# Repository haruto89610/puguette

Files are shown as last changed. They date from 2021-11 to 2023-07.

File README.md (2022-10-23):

# Puguette (パゲット)

[instagram](https://www.instagram.com/haruto89610/)

[photos](https://photos.app.goo.gl/W3VdmgdQKvAVjbRc6)

[twitter](https://twitter.com/TofuTohuman)

[Japanese](./README_jp.md)

[Youtube explanation in Japanese](https://www.youtube.com/watch?v=FokTPg63v5w)


|||
|:---|:---|
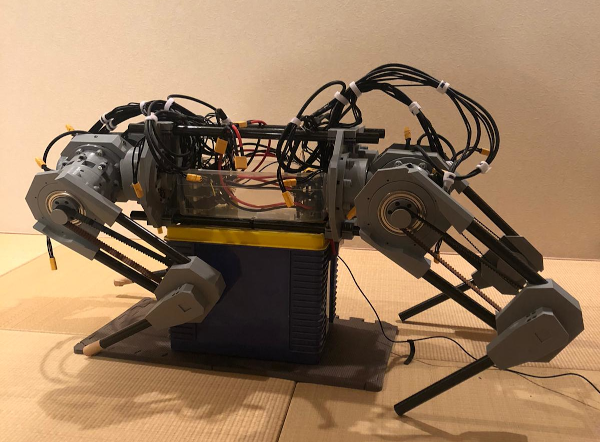
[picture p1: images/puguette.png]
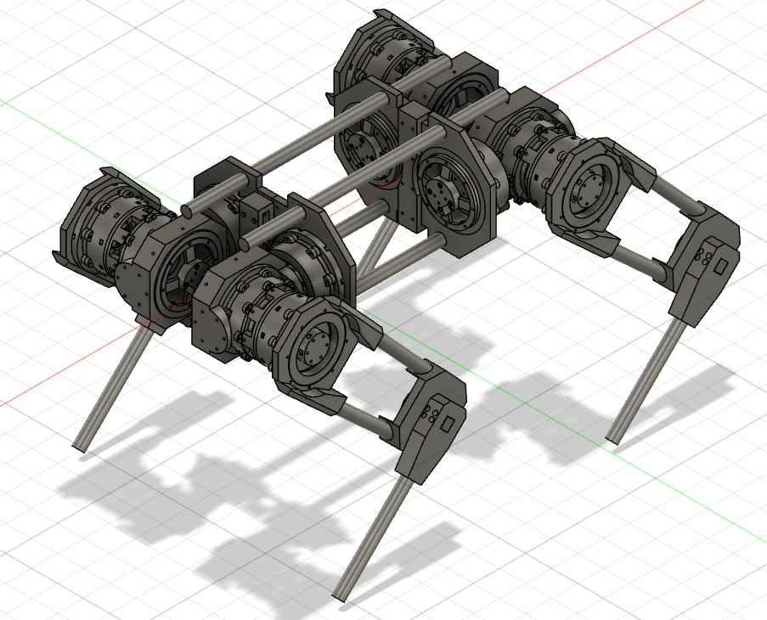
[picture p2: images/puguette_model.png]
|<p>(In progress)</p>|<p>(3D model)</p>|

## Introduction

Puguette is a fully open source 12 DOF quadruped robot. It stands at 80cm x 40cm x 60cm (when the legs are straight). It uses a BLDC motor for high torque efficiency and is coupled with a planetary gearbox to further increase said torque. The design is made to make small tweaks easy to change. For example, in order to change the gear ratio, just print the ring gear, planet gear and sun gear with the desired teeth count. Then mount that onto the motor holder. This can be done to the motor holder as well. To control Puguette, a Teensy 3.6, Jetson Nano, and 6 ODrives are used.

## Prototype

The older counterpart of Puguette, Spaghette, uses hobby servo motors. Similar to Puguette, it is 12 DOF and is fully 3D printed. In contrast to Puguette, Spaghette uses only an Arduino Mega to power it.

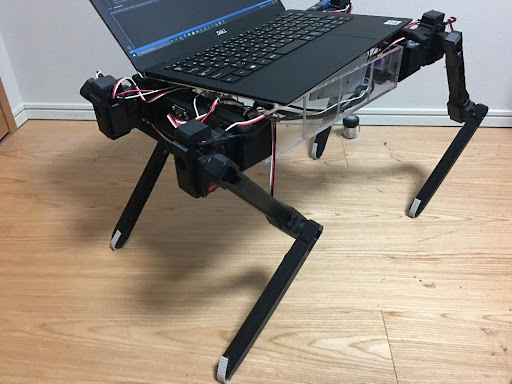
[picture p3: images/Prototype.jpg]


## Architecture

The Jetson Nano is the center of this robot. It communicates with the Teensy 3.6 via USB. The Teensy then communicates with all 6 ODrives using UART.

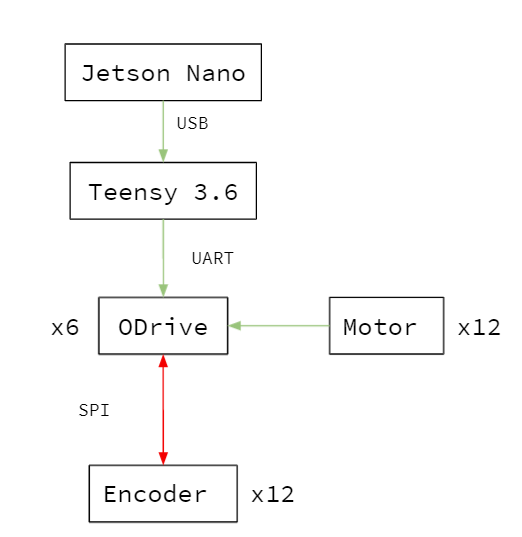
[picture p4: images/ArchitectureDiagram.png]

(architecture mindmap)

## Hardware Specification

There are 2 different (although similar) actuators designed. One for the x8318s motor, and one for the 8308 motor.
The total torque for each actuator is approx. 55Nm. The 8308 motor is connected to a 12:21 chain transmission system to further increase torque.

| Name | Unit | Description |
| :--- | :--- | :--- |
| X8318s motor | 4 | Upper leg actuator motor |
| 8308 motor | 8 | Lower and hip abductor actuator motor |
| ODrive driver | 6 | Controls motor |
| AS5048a encoder | 12 | Measures angle |
| Teensy microcontroller | 1 | Controls ODrive via UART |
| Bearing 6900ZZ | 4 | Bearing for Upper leg actuator |
| Bearing 6000ZZ | 36 | Bearing for planet gears |
| Bearing 6006ZZ | 4 | Bearing for lower joint  |
| Bearing 6010ZZ | 8 | Bearing for 8308 motor actuator |
| Lipo Battery | 3 | Power supply for the robot |

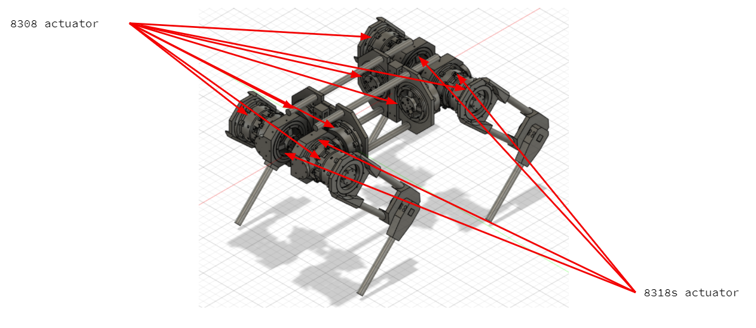
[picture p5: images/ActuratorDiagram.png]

(location of actuators)

## Actuator Assembly

  1. Mount encoder onto encoder holder using m2 screws.
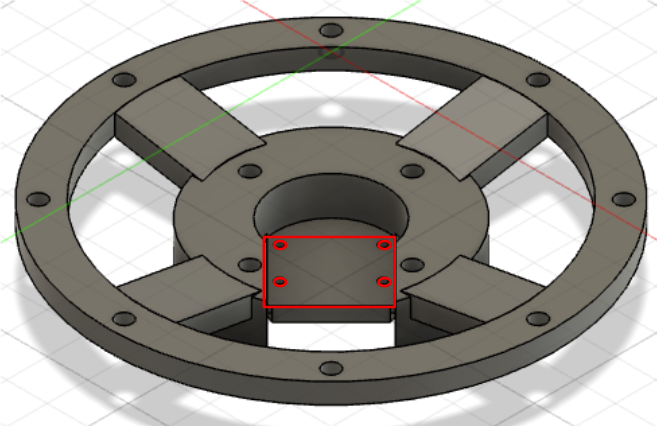
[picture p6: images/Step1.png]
  
  2. Mount the encoder magnet on the motor via the magnet holder.
  3. Insert m4 hex-nuts into the sides of motor holder.
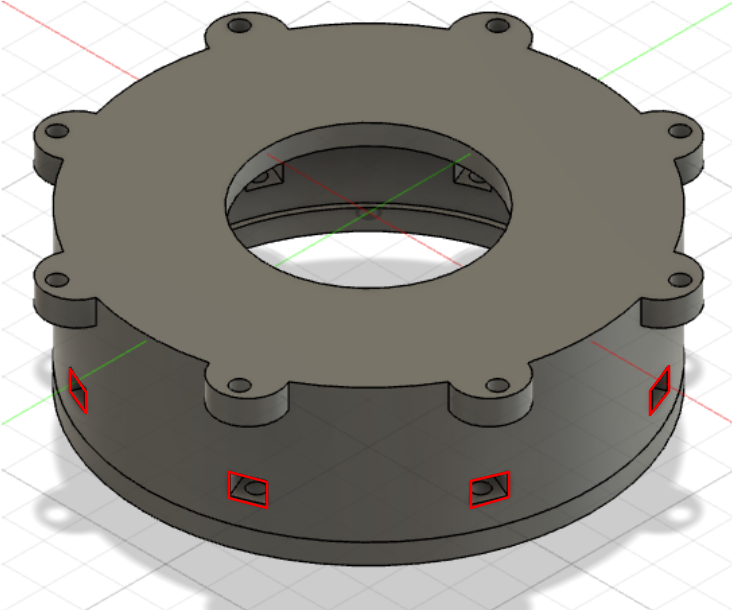
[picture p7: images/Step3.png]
  
  4. Screw encoder holder onto the motor holder via the holes.
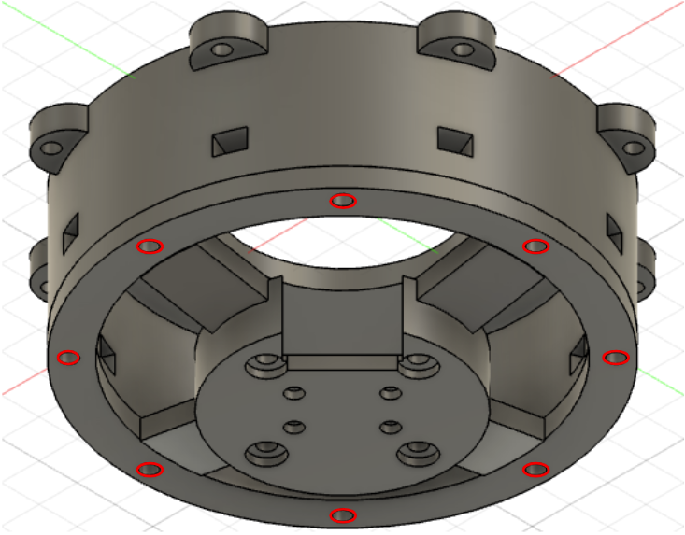
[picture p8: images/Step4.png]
  
  5. Place bearings onto the ring gear, and planet gear.
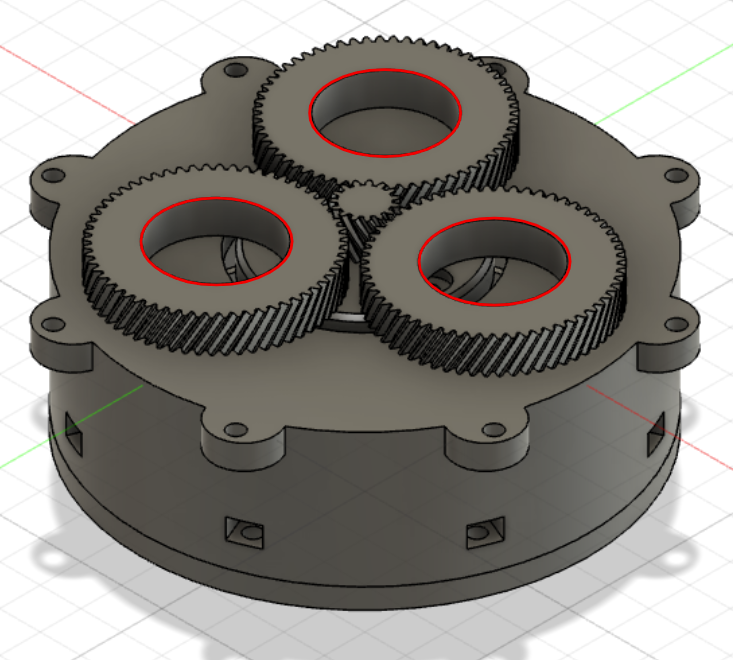
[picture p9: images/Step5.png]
  
  6. Push the planet gear onto the planet gear holder.
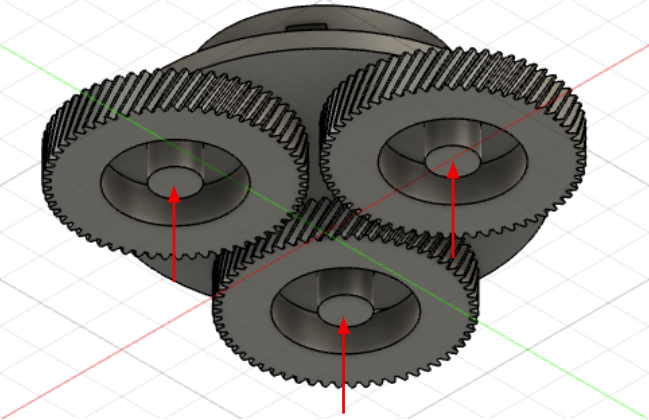
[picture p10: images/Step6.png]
  
  7. Mount the sun gear onto the motor via the opening on the motor holder.
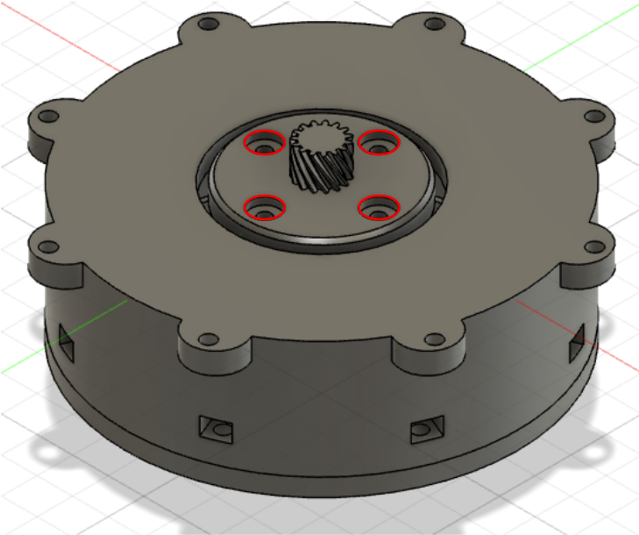
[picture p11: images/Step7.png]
  
  8. Push the sun gear into the center of the planet gear and planet gear holder.
  9. Push the ring gear on top of the planet gear holder.
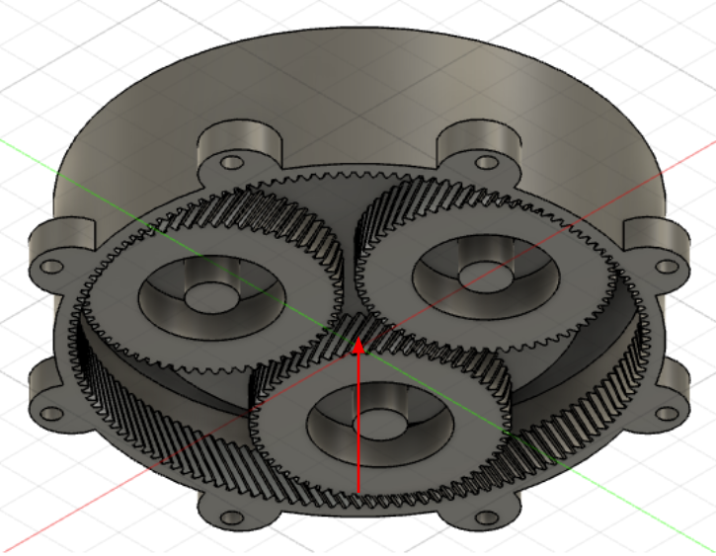
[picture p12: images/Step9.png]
  
  10. Mount motor holder onto ring gear.
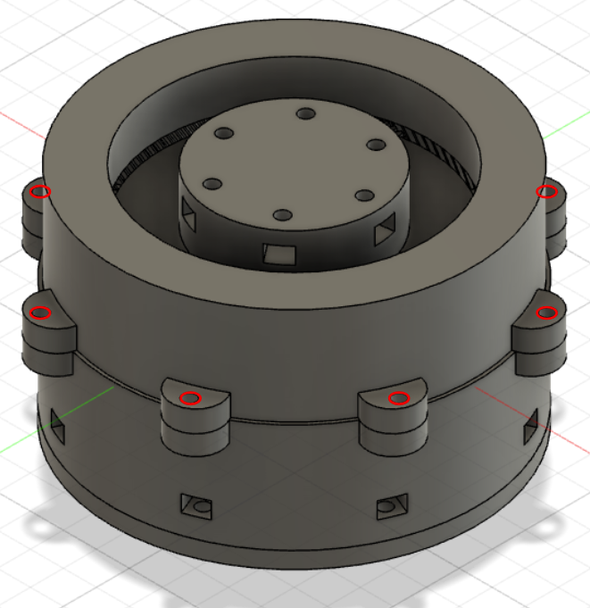
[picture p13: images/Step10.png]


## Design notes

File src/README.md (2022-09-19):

## Software and Simulation

The robot has went through different versions with different architectures. The old version aimed to use a Jetson Nano as well as a Teensy to control the 6 ODrives. As a result, part of the code was written in C++ as well as Python. However, errors were encountered where the UART signals had incorrect values. This could possibly have originated from noise, or the large amount of information needed to be transmitted. Although lowering the baudrate resulted in cleaner results, completely removing the issue was a difficult problem to overcome. As a result, the Teensy was removed, and the Jetson Nano communicates directly with the ODrives via USB. The new program uses only Python.

Because testing the robot is not always easy, considering the sheer size of the robot, a PyBullet simulation was made to attempt to help with testing. Because the polygon count on the actual CAD is too high, rendering the model was an issue. To solve this issue, the simulation uses a simplified version of the CAD model.

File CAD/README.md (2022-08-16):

## Updates

The first iteration of the actuator had many flaws. One of these major flaws was that many parts would break as a result of torsional stress. Most notably, the sun gear, and the planet gear carrier. To counter this, the second iteration of the actuator uses chrome gears to replace the PLA sun gears. These chrome gears have 15 teeth and a gear module of 0.8 (https://www.monotaro.com/p/3682/5512/?t.attr_f957=0.8&t.attr_f958=15&t.q=%83M%83A). As some motors do not have a shaft for the gears to attach to, a sun gear adapter was created to counter this issue. As for the planet gear carriers, the part was split into two different models. The Planet Carrier Bottom connects to the Planet Carrier Top with the planet gear in between. These two parts can then be screwed in place with an M4 screw. Overall, the issue main issue with the first iteration was that the actuator broke under high torque.

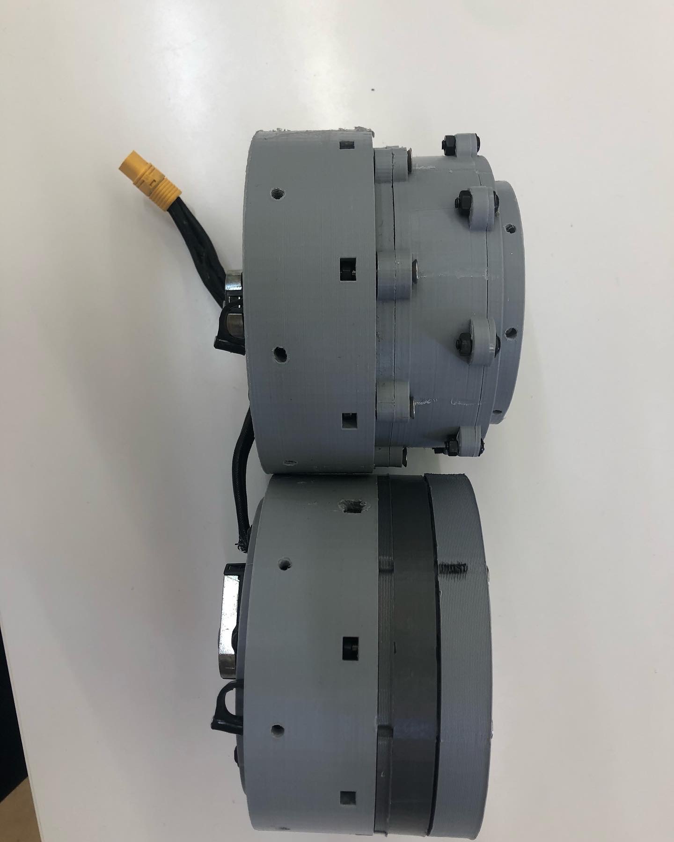
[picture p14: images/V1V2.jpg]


First test of Actuator V2:
https://www.instagram.com/p/Cg_KBtlJQmC/

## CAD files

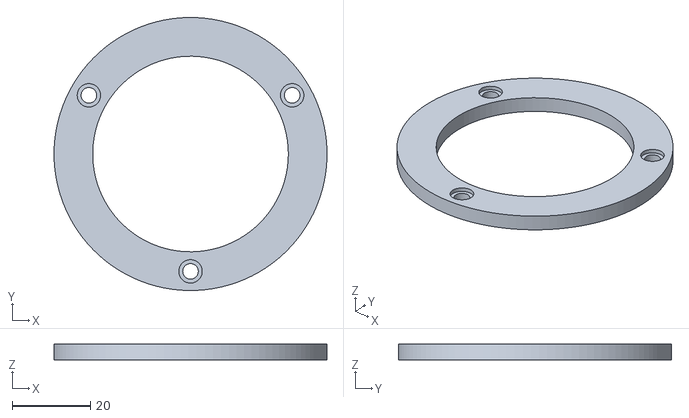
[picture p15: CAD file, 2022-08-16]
CAD/Actuator V2/8308 actuator V2/Planet Carrier Bottom v3.stl
69.8 x 69.8 x 4.00

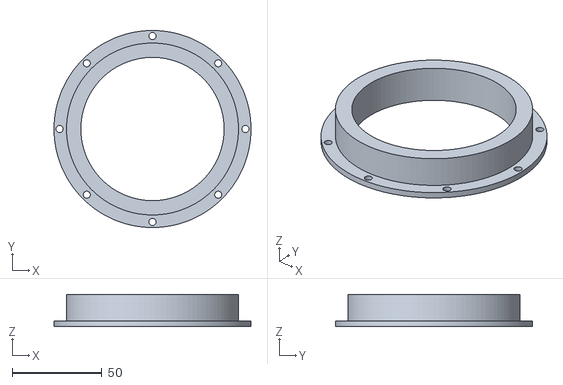
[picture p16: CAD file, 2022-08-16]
CAD/Actuator V2/8318 actuator V2/Ring Gear Cover v7.stl
110.0 x 110.0 x 18.0

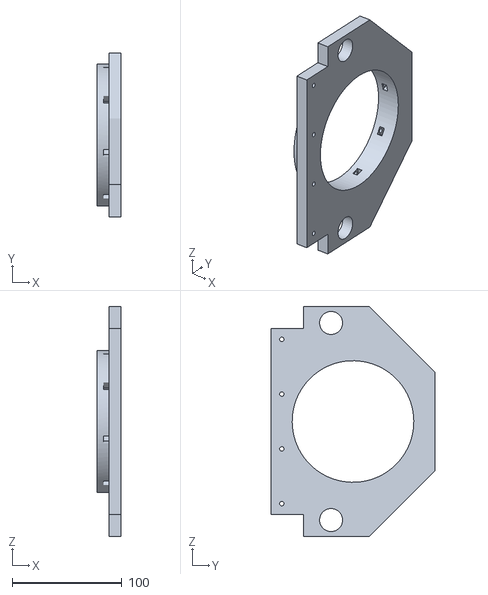
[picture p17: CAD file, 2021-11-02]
CAD/Hip mechanism/Hip Actuator Holder.stl
22.0 x 150.0 x 210.0

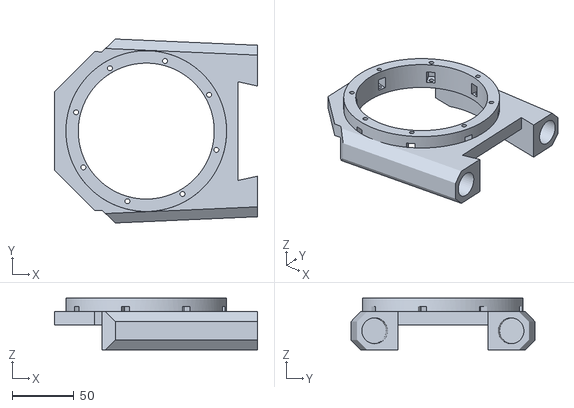
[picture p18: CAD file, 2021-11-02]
CAD/Leg/Upper Leg Holder.stl
164.2 x 148.8 x 42.0

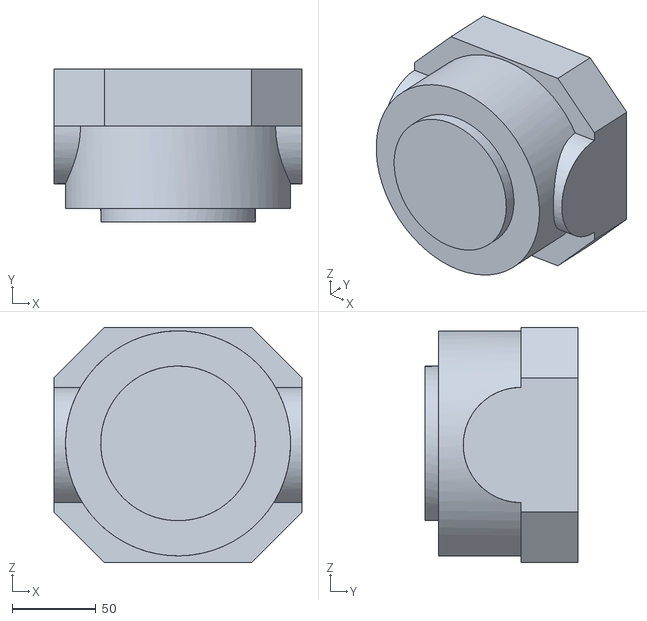
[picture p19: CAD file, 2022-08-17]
src/PyBullet Simulation/meshes/BL_Joint1.stl
147.7 x 91.0 x 140.0

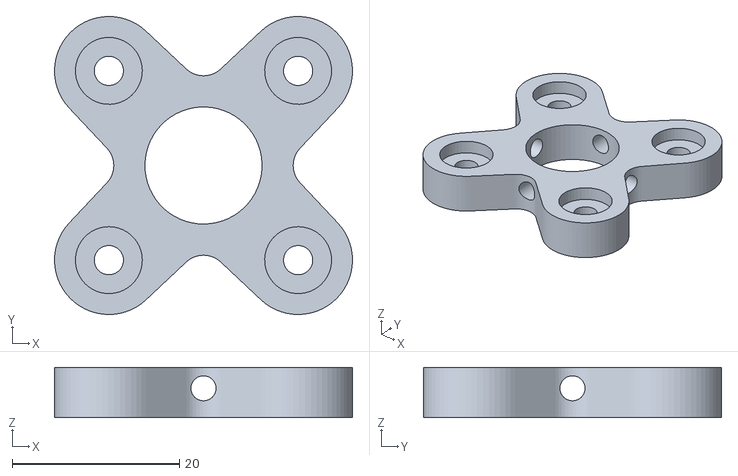
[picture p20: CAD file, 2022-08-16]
CAD/Actuator V2/8308 actuator V2/Sun Gear Adapter v3.stl
35.6 x 35.6 x 6.00

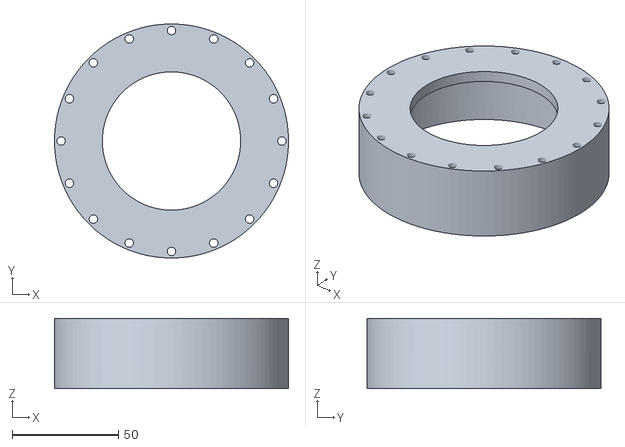
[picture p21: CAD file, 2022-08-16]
CAD/Actuator V2/8318 actuator V2/Motor Holder v6.stl
110.0 x 110.0 x 33.0

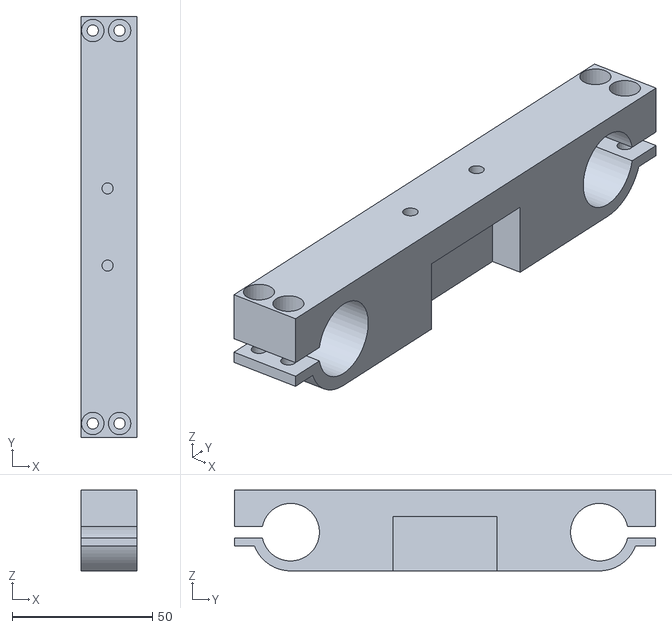
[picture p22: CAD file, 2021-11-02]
CAD/Hip mechanism/Hip Rod Support.stl
20.0 x 150.0 x 28.8

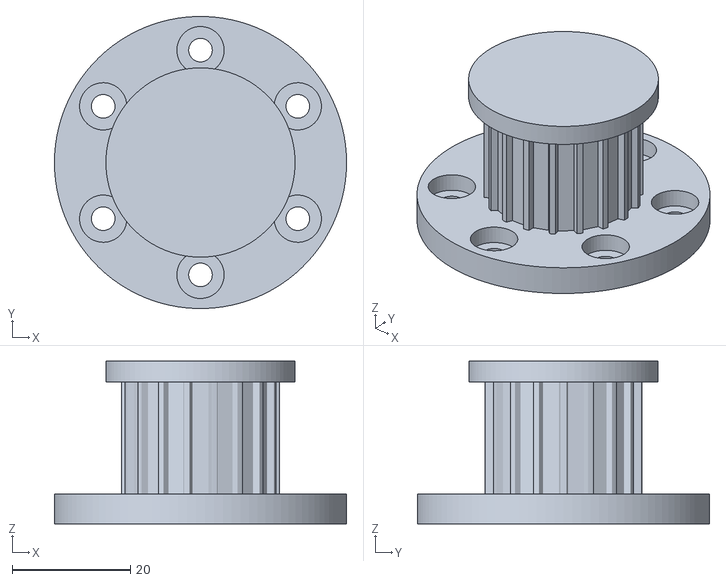
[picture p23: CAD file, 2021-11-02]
CAD/Leg/Upper Leg Timing Pulley.stl
49.4 x 49.4 x 27.5

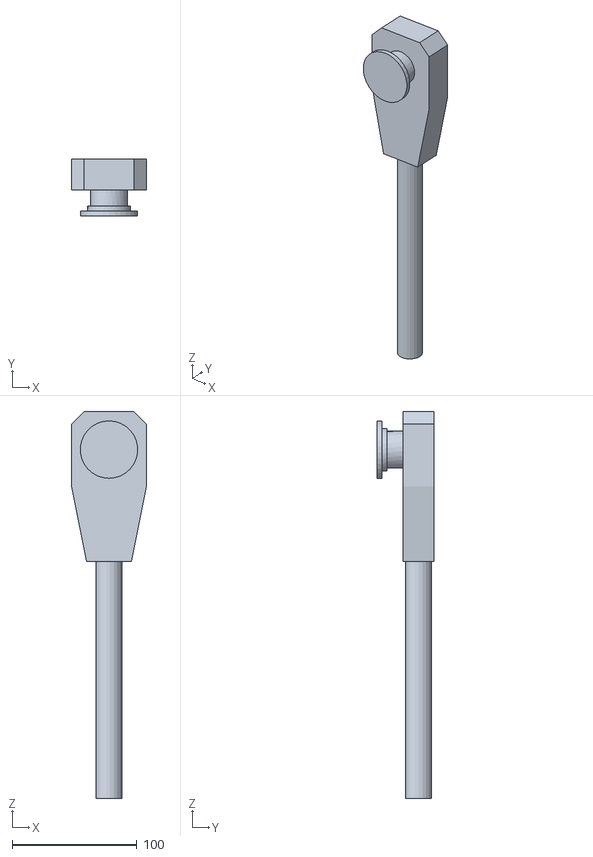
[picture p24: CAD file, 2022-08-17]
src/PyBullet Simulation/meshes/FR_Lower_Leg1.stl
60.0 x 46.0 x 310.0

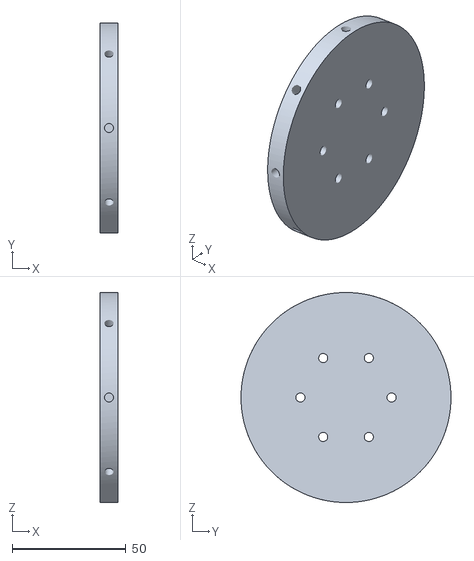
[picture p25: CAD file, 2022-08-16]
CAD/Actuator V2/8308 actuator V2/Lower Leg Actuator Holder 8318 v3.stl
8.00 x 92.1 x 92.1

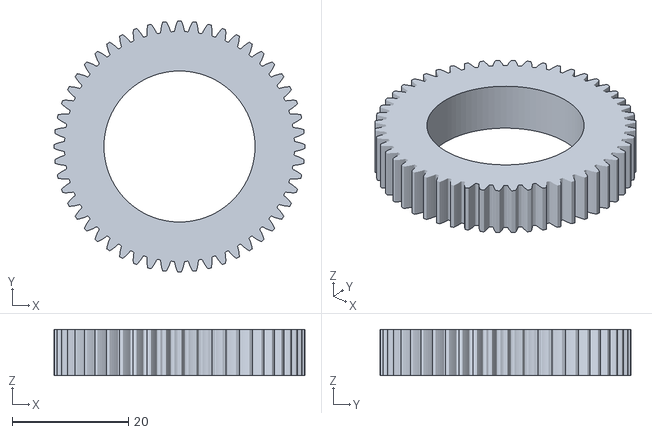
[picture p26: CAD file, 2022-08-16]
CAD/Actuator V2/8318 actuator V2/Planet Gear v2.stl
43.2 x 43.2 x 8.00

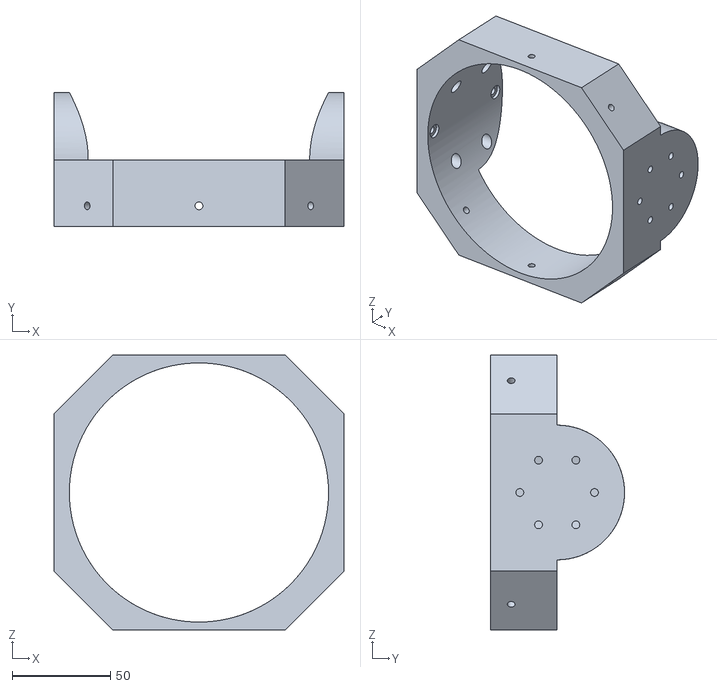
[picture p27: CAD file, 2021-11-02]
CAD/Hip mechanism/Upper Leg Actuator Holder.stl
147.7 x 68.3 x 140.0

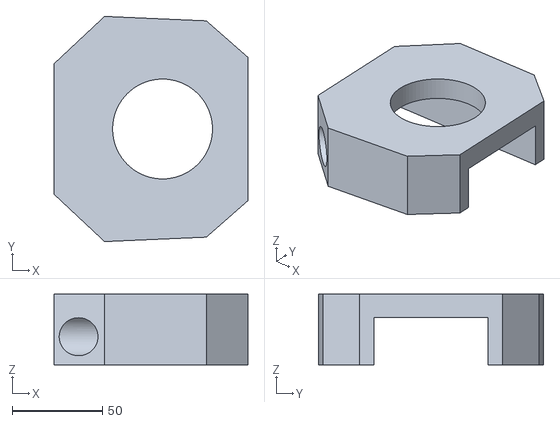
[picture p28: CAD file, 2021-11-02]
CAD/Leg/Lower Leg Holder.stl
107.2 x 124.5 x 39.0

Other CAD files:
src/PyBullet Simulation/meshes/BR_Joint1.stl
CAD/Actuator V2/8308 actuator V2/Ring Gear Cover v5.stl
CAD/Actuator V2/8318 actuator V2/Planet Gear Carrier Top v4.stl
CAD/Hip mechanism/Actuator Holder.stl
CAD/Actuator V1/8308 actuator/Encoder Holder 8308.stl
CAD/Actuator V1/8308 actuator/Motor Holder 8308.stl
CAD/Actuator V1/8308 actuator/Planet Gear 1, 10.stl
CAD/Actuator V1/8308 actuator/Planet Gear Holder 8308.stl
CAD/Actuator V1/8308 actuator/Planetary Gearbox 8308.stl
CAD/Actuator V1/8308 actuator/Ring Gear 1,10 8308.stl
CAD/Actuator V1/8308 actuator/Sun Gear 1,10.stl
CAD/Actuator V1/8308 actuator/magnet holder 8308.stl
CAD/Actuator V1/8318 actuator/Encoder Holder 8318.stl
CAD/Actuator V1/8318 actuator/Magnet holder 8318.stl
CAD/Actuator V1/8318 actuator/Motor Holder 8318.stl
CAD/Actuator V1/8318 actuator/Planet Gear 1, 10.stl
CAD/Actuator V1/8318 actuator/Planet Gear Holder 8318.stl
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

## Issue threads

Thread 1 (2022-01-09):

Timing belt skipping

haruto89610, 2022-01-09:
The timing belt used to control the lower leg skips when under high torque.

Closed 2022-04-01.

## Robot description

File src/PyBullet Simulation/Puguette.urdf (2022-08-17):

<?xml version="1.0" ?>
<robot name="Puguette">

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

<link name="base_link">
  <inertial>
    <origin xyz="-0.03180841476638693 0.07427733536146494 -0.001579457934195628" rpy="0 0 0"/>
    <mass value="12"/>
    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
  </inertial>
  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
</link>

<link name="FR_Joint1">
  <inertial>
    <origin xyz="-0.07386142547452285 0.0065706579307107105 0.0004947012899105428" rpy="0 0 0"/>
    <mass value="1.2"/>
    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
  </inertial>
  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
</link>

<link name="FR_Upper_Leg1">
  <inertial>
    <origin xyz="0.00020261207237287637 0.07283703782473894 -0.06601468887803173" rpy="0 0 0"/>
    <mass value="1.2"/>
    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
  </inertial>
  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
</link>

<link name="FR_Lower_Leg1">
  <inertial>
    <origin xyz="-1.1094217650109428e-07 0.010539661618046203 -0.06653363488178754" rpy="0 0 0"/>
    <mass value="1.2"/>
    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
  </inertial>
  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
</link>

<link name="FL_Joint1">
  <inertial>
    <origin xyz="-0.07386142620000508 -0.006569979700954141 -0.0004952540320456731" rpy="0 0 0"/>
    <mass value="1.2"/>
    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
  </inertial>
  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
</link>

<link name="FL_Upper_Leg1">
  <inertial>
    <origin xyz="-0.000203213226204646 -0.07283635959498225 -0.06601498909918865" rpy="0 0 0"/>
    <mass value="1.2"/>
    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
  </inertial>
  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
</link>

<link name="FL_Lower_Leg1">
  <inertial>
    <origin xyz="-4.902062988865197e-07 -0.01053998338829007 -0.06653293510135605" rpy="0 0 0"/>
    <mass value="1.2"/>
    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
  </inertial>
  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
</link>

<link name="BL_Joint1">
  <inertial>
    <origin xyz="0.07386125382469919 -0.00656997970095369 0.0004947012899100759" rpy="0 0 0"/>
    <mass value="1.2"/>
    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
  </inertial>
  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
</link>

<link name="BL_Upper_Leg1">
  <inertial>
    <origin xyz="-0.0002027837275550004 -0.07283635959498128 -0.06601468887962054" rpy="0 0 0"/>
    <mass value="1.2"/>
    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
  </inertial>
  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
</link>

<link name="BL_Lower_Leg1">
  <inertial>
    <origin xyz="-6.069636965255754e-08 -0.010539983396232466 -0.06653363490149644" rpy="0 0 0"/>
    <mass value="1.2"/>
    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
  </inertial>
  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
</link>

<link name="BR_Joint1">
  <inertial>
    <origin xyz="0.07386125309921679 0.006570657930710683 -0.0004952540320459554" rpy="0 0 0"/>
    <mass value="1.2"/>
    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
  </inertial>
  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
</link>

<link name="BR_Upper_Leg1">
  <inertial>
    <origin xyz="0.00020304012542721184 0.07283703782473855 -0.06601498909918857" rpy="0 0 0"/>
    <mass value="1.2"/>
    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
  </inertial>
  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
</link>

<link name="BR_Lower_Leg1">
  <inertial>
    <origin xyz="3.132389264082214e-07 0.010539661365388864 -0.06653294310138463" rpy="0 0 0"/>
    <mass value="1.2"/>
    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
  </inertial>
  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
</link>

<joint name="Rev53" type="revolute">
  <origin xyz="-0.254809 0.149277 -0.001579" rpy="0 0 0"/>
  <parent link="base_link"/>
  <child link="FR_Joint1"/>
  <axis xyz="-1.0 -0.0 0.0"/>
  <limit upper="1.570796" lower="-1.570796" effort="100" velocity="100"/>
</joint>
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

<joint name="Rev57" type="continuous">
  <origin xyz="-0.073879 0.04903 0.000966" rpy="0 0 0"/>
  <parent link="FR_Joint1"/>
  <child link="FR_Upper_Leg1"/>
  <axis xyz="-0.0 -1.0 0.0"/>
</joint>
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

<joint name="Rev65" type="continuous">
  <origin xyz="0.0 0.128036 -0.280013" rpy="0 0 0"/>
  <parent link="FR_Upper_Leg1"/>
  <child link="FR_Lower_Leg1"/>
  <axis xyz="-0.0 -1.0 0.0"/>
</joint>
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

<joint name="Rev69" type="revolute">
  <origin xyz="-0.254809 -0.000723 -0.001579" rpy="0 0 0"/>
  <parent link="base_link"/>
  <child link="FL_Joint1"/>
  <axis xyz="-1.0 -0.0 0.0"/>
  <limit upper="1.570796" lower="-1.570796" effort="100" velocity="100"/>
</joint>
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

<joint name="Rev70" type="continuous">
  <origin xyz="-0.073879 -0.04903 -0.000967" rpy="0 0 0"/>
  <parent link="FL_Joint1"/>
  <child link="FL_Upper_Leg1"/>
  <axis xyz="0.0 1.0 -0.0"/>
</joint>
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

<joint name="Rev71" type="continuous">
  <origin xyz="0.0 -0.128035 -0.280014" rpy="0 0 0"/>
  <parent link="FL_Upper_Leg1"/>
  <child link="FL_Lower_Leg1"/>
  <axis xyz="0.0 1.0 -0.0"/>
</joint>
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

<joint name="Rev72" type="revolute">
  <origin xyz="0.191192 -0.000723 -0.001579" rpy="0 0 0"/>
  <parent link="base_link"/>
  <child link="BL_Joint1"/>
  <axis xyz="1.0 0.0 0.0"/>
  <limit upper="1.570796" lower="-1.570796" effort="100" velocity="100"/>
</joint>
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

<joint name="Rev73" type="continuous">
  <origin xyz="0.073879 -0.04903 0.000966" rpy="0 0 0"/>
  <parent link="BL_Joint1"/>
  <child link="BL_Upper_Leg1"/>
  <axis xyz="0.0 1.0 0.0"/>
</joint>
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

<joint name="Rev74" type="continuous">
  <origin xyz="0.0 -0.128035 -0.280013" rpy="0 0 0"/>
  <parent link="BL_Upper_Leg1"/>
  <child link="BL_Lower_Leg1"/>
  <axis xyz="0.0 1.0 0.0"/>
</joint>
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

<joint name="Rev75" type="revolute">
  <origin xyz="0.191192 0.149277 -0.001579" rpy="0 0 0"/>
  <parent link="base_link"/>
  <child link="BR_Joint1"/>
  <axis xyz="1.0 0.0 0.0"/>
  <limit upper="1.570796" lower="-1.570796" effort="100" velocity="100"/>
</joint>
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

<joint name="Rev76" type="continuous">
  <origin xyz="0.073879 0.04903 -0.000967" rpy="0 0 0"/>
  <parent link="BR_Joint1"/>
  <child link="BR_Upper_Leg1"/>
  <axis xyz="-0.0 -1.0 -0.0"/>
</joint>
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

<joint name="Rev77" type="continuous">
  <origin xyz="0.0 0.128036 -0.280014" rpy="0 0 0"/>
  <parent link="BR_Upper_Leg1"/>
  <child link="BR_Lower_Leg1"/>
  <axis xyz="-0.0 -1.0 -0.0"/>
</joint>
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

</robot>

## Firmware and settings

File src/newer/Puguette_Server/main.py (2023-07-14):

import sys
import odrive
import threading
import can
import struct
import socket
import time
import numpy as np
from odrive.enums import *
from enum import Enum

from Gaits import Walk
from Gaits.Walk import ratio, xPoints, zPoints
from Kinematics import Model

struct_format = ">6f14?"

can_front = can.interface.Bus(channel='can0', bustype='socketcan')
can_back = can.interface.Bus(channel='can1', bustype='socketcan')

class Commands(Enum): #ODrive CAN cmd_id
    EMERGENCY_STOP = 0x002
    MOTOR_ERROR = 0x003
    ENCODER_ERROR = 0x004
    AXIS_REQUESTED_STATE = 0x007
    ENCODER_COUNT = 0x00A
    INPUT_POS = 0x00C
    REBOOT = 0x016
    VBUS_VOLTAGE = 0x017
    CLEAR_ERRORS = 0x018
    LINEAR_COUNT = 0x019

class State(Enum): #ODrive CAN data
    IDLE = 1
    FULL_CALIBRATION_SEQUENCE = 3
    CLOSED_LOOP_CONTROL = 8

class Joint(Enum): #Axis ID
    FL_hip = 0
    FL_upper = 1
    FL_lower = 2
    FR_hip = 3
    FR_upper = 4
    FR_lower = 5
    BL_hip = 6
    BL_upper = 7
    BL_lower = 8
    BR_hip = 9
    BR_upper = 10
    BR_lower = 11

def odrive_can_cmd(node_id, cmd_id, data=[], format=''): #convert to arbitration ID
    data_frame = struct.pack(format, *data)
    msg = can.Message(arbitration_id=((node_id << 5) | cmd_id), data=data_frame, is_extended_id=False)
#    if node_id < 6:
    can_front.send(msg)
#    elif node_id >= 6:
    can_back.send(msg)

"""
def odrive_getPos(node_id):
    while(1):
        msg = can_bus.recv()
        if(msg.arbitration_id == (node_id << 5) + 0x9):
            data = struct.unpack('ff', msg.data)
            return data[0]
"""

controller_state_available = threading.Event()

def socket_server(): #set up server
    global controller_state
    HOST = "10.0.0.27"
    PORT = 65432
    with socket.socket(socket.AF_INET, socket.SOCK_STREAM) as s:
        s.bind((HOST, PORT))
        s.listen()
        conn, addr = s.accept()
        with conn:
            print(f"Connected by {addr}")
            previous_controller_state = 0
            while True:
                data = conn.recv(4096)
                if len(data) == struct.calcsize(struct_format):
                    controller_state = struct.unpack(struct_format, data)
                    previous_controller_state = controller_state
                    controller_state_available.set()
                else:
                    controller_state = previous_controller_state
                    controller_state_available.set()


def main():
    T= 0.00
    coords = np.array([[0.00, -0.10, -0.40],
                       [0.00,  0.10, -0.40],
                       [0.00, -0.10, -0.40],
                       [0.00,  0.10, -0.40]])
    rotations = np.array([0.00, 0.00, 0.00])
    translations = np.array([0.00, 0.00, 0.00])

    speed, angle, pitch, roll, yaw = 0.00, 0.00, 0.00, 0.00, 0.00
    while True:
        controller_state_available.wait()
        time.sleep(0.01)
        speed = controller_state[0]
        angle = controller_state[1]
        pitch = controller_state[2]
        roll = controller_state[3]
        yaw = controller_state[4] + controller_state[5]

        linear_count_check = 0

        for member in list(Joint):

#            print(f"received {T, controller_state[0], Model.Kinematic_Model(coords, rotations, translations)[int(member.value/3)][0][member.value%3]}")
            #-------------CONTROLLER STATES-------------#

            if controller_state[12] == True:
#                #FL
                odrive_can_cmd(Joint.FL_hip.value, Commands.AXIS_REQUESTED_STATE.value, [State.IDLE.value], 'h')
                odrive_can_cmd(Joint.FL_upper.value, Commands.AXIS_REQUESTED_STATE.value, [State.IDLE.value], 'h')
                odrive_can_cmd(Joint.FL_lower.value, Commands.AXIS_REQUESTED_STATE.value, [State.IDLE.value], 'h')
#                #FR
                odrive_can_cmd(Joint.FR_hip.value, Commands.AXIS_REQUESTED_STATE.value, [State.IDLE.value], 'h')
                odrive_can_cmd(Joint.FR_upper.value, Commands.AXIS_REQUESTED_STATE.value, [State.IDLE.value], 'h')
                odrive_can_cmd(Joint.FR_lower.value, Commands.AXIS_REQUESTED_STATE.value, [State.IDLE.value], 'h')
#                #BL
                odrive_can_cmd(Joint.BL_hip.value, Commands.AXIS_REQUESTED_STATE.value, [State.IDLE.value], 'h')
                odrive_can_cmd(Joint.BL_upper.value, Commands.AXIS_REQUESTED_STATE.value, [State.IDLE.value], 'h')
                odrive_can_cmd(Joint.BL_lower.value, Commands.AXIS_REQUESTED_STATE.value, [State.IDLE.value], 'h')
#                #BR
                odrive_can_cmd(Joint.BR_hip.value, Commands.AXIS_REQUESTED_STATE.value, [State.IDLE.value], 'h')
                odrive_can_cmd(Joint.BR_upper.value, Commands.AXIS_REQUESTED_STATE.value, [State.IDLE.value], 'h')
                odrive_can_cmd(Joint.BR_lower.value, Commands.AXIS_REQUESTED_STATE.value, [State.IDLE.value], 'h')
                print(member.value)
            elif controller_state[13] == True:
#                #FL
                odrive_can_cmd(Joint.FL_hip.value, Commands.AXIS_REQUESTED_STATE.value, [State.CLOSED_LOOP_CONTROL.value], 'h')
                odrive_can_cmd(Joint.FL_upper.value, Commands.AXIS_REQUESTED_STATE.value, [State.CLOSED_LOOP_CONTROL.value], 'h')
                odrive_can_cmd(Joint.FL_lower.value, Commands.AXIS_REQUESTED_STATE.value, [State.CLOSED_LOOP_CONTROL.value], 'h')
#                #FR
                odrive_can_cmd(Joint.FR_hip.value, Commands.AXIS_REQUESTED_STATE.value, [State.CLOSED_LOOP_CONTROL.value], 'h')
                odrive_can_cmd(Joint.FR_upper.value, Commands.AXIS_REQUESTED_STATE.value, [State.CLOSED_LOOP_CONTROL.value], 'h')
                odrive_can_cmd(Joint.FR_lower.value, Commands.AXIS_REQUESTED_STATE.value, [State.CLOSED_LOOP_CONTROL.value], 'h')
#                #BL
                odrive_can_cmd(Joint.BL_hip.value, Commands.AXIS_REQUESTED_STATE.value, [State.CLOSED_LOOP_CONTROL.value], 'h')
                odrive_can_cmd(Joint.BL_upper.value, Commands.AXIS_REQUESTED_STATE.value, [State.CLOSED_LOOP_CONTROL.value], 'h')
                odrive_can_cmd(Joint.BL_lower.value, Commands.AXIS_REQUESTED_STATE.value, [State.CLOSED_LOOP_CONTROL.value], 'h')
#                #BR
                odrive_can_cmd(Joint.BR_hip.value, Commands.AXIS_REQUESTED_STATE.value, [State.CLOSED_LOOP_CONTROL.value], 'h')
                odrive_can_cmd(Joint.BR_upper.value, Commands.AXIS_REQUESTED_STATE.value, [State.CLOSED_LOOP_CONTROL.value], 'h')
                odrive_can_cmd(Joint.BR_lower.value, Commands.AXIS_REQUESTED_STATE.value, [State.CLOSED_LOOP_CONTROL.value], 'h')
                print(member.value)
            elif controller_state[14] == True:
#                #FL
                odrive_can_cmd(Joint.FL_hip.value, Commands.AXIS_REQUESTED_STATE.value, [State.FULL_CALIBRATION_SEQUENCE.value], 'h')
                odrive_can_cmd(Joint.FL_upper.value, Commands.AXIS_REQUESTED_STATE.value, [State.FULL_CALIBRATION_SEQUENCE.value], 'h')
                odrive_can_cmd(Joint.FL_lower.value, Commands.AXIS_REQUESTED_STATE.value, [State.FULL_CALIBRATION_SEQUENCE.value], 'h')
#                #FR
                odrive_can_cmd(Joint.FR_hip.value, Commands.AXIS_REQUESTED_STATE.value, [State.FULL_CALIBRATION_SEQUENCE.value], 'h')
                odrive_can_cmd(Joint.FR_upper.value, Commands.AXIS_REQUESTED_STATE.value, [State.FULL_CALIBRATION_SEQUENCE.value], 'h')
                odrive_can_cmd(Joint.FR_lower.value, Commands.AXIS_REQUESTED_STATE.value, [State.FULL_CALIBRATION_SEQUENCE.value], 'h')
#                #BL
                odrive_can_cmd(Joint.BL_hip.value, Commands.AXIS_REQUESTED_STATE.value, [State.FULL_CALIBRATION_SEQUENCE.value], 'h')
                odrive_can_cmd(Joint.BL_upper.value, Commands.AXIS_REQUESTED_STATE.value, [State.FULL_CALIBRATION_SEQUENCE.value], 'h')
                odrive_can_cmd(Joint.BL_lower.value, Commands.AXIS_REQUESTED_STATE.value, [State.FULL_CALIBRATION_SEQUENCE.value], 'h')
#                #BR
                odrive_can_cmd(Joint.BR_hip.value, Commands.AXIS_REQUESTED_STATE.value, [State.FULL_CALIBRATION_SEQUENCE.value], 'h')
                odrive_can_cmd(Joint.BR_upper.value, Commands.AXIS_REQUESTED_STATE.value, [State.FULL_CALIBRATION_SEQUENCE.value], 'h')
                odrive_can_cmd(Joint.BR_lower.value, Commands.AXIS_REQUESTED_STATE.value, [State.FULL_CALIBRATION_SEQUENCE.value], 'h')
                print(member.value)

            #----------------CALIBRATION----------------#
            elif controller_state[19] == True:
                print("hip calibration")
                odrive_can_cmd(Joint.FL_hip.value, Commands.LINEAR_COUNT.value, [0], 'h')
                odrive_can_cmd(Joint.FR_hip.value, Commands.LINEAR_COUNT.value, [0], 'h')
                odrive_can_cmd(Joint.BL_hip.value, Commands.LINEAR_COUNT.value, [0], 'h')
                odrive_can_cmd(Joint.BR_hip.value, Commands.LINEAR_COUNT.value, [0], 'h')
#                for i in range(3):
#                    #HIPS
#                    odrive_can_cmd(3*i, Commands.LINEAR_COUNT.value, [0], 'h')
#                    i+=1
            elif controller_state[17] == True:
                odrive_can_cmd(Joint.FL_upper.value, Commands.LINEAR_COUNT.value, [0], 'h')
                odrive_can_cmd(Joint.FR_upper.value, Commands.LINEAR_COUNT.value, [0], 'h')
                odrive_can_cmd(Joint.BL_upper.value, Commands.LINEAR_COUNT.value, [0], 'h')
                odrive_can_cmd(Joint.BR_upper.value, Commands.LINEAR_COUNT.value, [0], 'h')
                print("upper leg calibration")
#                for i in range(3):
#                    odrive_can_cmd(3*i+1, Commands.LINEAR_COUNT.value, [0], 'h')
#                    i+=1
            elif controller_state[16] == True:
                print("lower leg calibration")
                odrive_can_cmd(Joint.FL_lower.value, Commands.LINEAR_COUNT.value, [0], 'h')
                odrive_can_cmd(Joint.FR_lower.value, Commands.LINEAR_COUNT.value, [0], 'h')
                odrive_can_cmd(Joint.BL_lower.value, Commands.LINEAR_COUNT.value, [0], 'h')
                odrive_can_cmd(Joint.BR_lower.value, Commands.LINEAR_COUNT.value, [0], 'h')
#                for i in range(3):
#                    odrive_can_cmd(3*i+2, Commands.LINEAR_COUNT.value, [0], 'h')
#                    i+=1

            #-------------------GAITS-------------------#
            if speed != 0 or angle != 0:
                if T <= 0:
                    T = 2
                elif T <= 1:
                    coords[0][0], coords[0][2] = Walk.bezier(T) #FR
                    coords[0][2] = coords[0][2]

                    coords[3][0], coords[3][2] = Walk.bezier(1-T) #BL
                    coords[3][2] = coords[3][2]

                    coords[1][0], coords[1][2] = ((-xPoints[11]/ratio)+(xPoints[0]/ratio))*T+xPoints[11]/ratio, -0.4 #FL
                    coords[2][0], coords[2][2] = ((xPoints[11]/ratio)-(xPoints[0]/ratio))*T+xPoints[0]/ratio, -0.4 #BR

                    T+=speed
                elif T > 1 and T <= 2:
                    coords[1][0], coords[1][2] = Walk.bezier(T-1)
                    coords[1][2] = coords[1][2]

                    coords[2][0], coords[2][2] = Walk.bezier(2-T)
                    coords[2][2] = coords[2][2]

                    coords[0][0], coords[0][2] = ((-xPoints[11]/ratio)+(xPoints[0]/ratio))*(T-1)+xPoints[11]/ratio, -0.4
                    coords[3][0], coords[3][2] = ((xPoints[11]/ratio)-(xPoints[0]/ratio))*(T-1)+xPoints[0]/ratio, -0.4

                    T+=speed
                elif T > 2:
                    T-=2
            elif pitch != 0 or roll != 0 or yaw != 0:
                rotations[0] = roll
                rotations[1] = pitch
                rotations[2] = yaw

            else:
                coords = np.array([[0.00, -0.10, -0.40],
                                   [0.00,  0.10, -0.40],
                                   [0.00, -0.10, -0.40],
                                   [0.00,  0.10, -0.40]])
                rotations = np.array([0.00, 0.00, 0.00])
                translations = np.array([0.00, 0.00, 0.00])

#            #FL
            odrive_can_cmd(Joint.FL_hip.value, Commands.INPUT_POS.value, [Model.Kinematic_Model(coords, rotations, translations)[1][0][0], 0, 0], 'fhh')
            odrive_can_cmd(Joint.FL_upper.value, Commands.INPUT_POS.value, [Model.Kinematic_Model(coords, rotations, translations)[1][0][1], 0, 0], 'fhh')
            odrive_can_cmd(Joint.FL_lower.value, Commands.INPUT_POS.value, [Model.Kinematic_Model(coords, rotations, translations)[1][0][2], 0, 0], 'fhh')
#            #FR
            odrive_can_cmd(Joint.FR_hip.value, Commands.INPUT_POS.value, [Model.Kinematic_Model(coords, rotations, translations)[0][0][0], 0, 0], 'fhh')
            odrive_can_cmd(Joint.FR_upper.value, Commands.INPUT_POS.value, [Model.Kinematic_Model(coords, rotations, translations)[0][0][1], 0, 0], 'fhh')
            odrive_can_cmd(Joint.FR_lower.value, Commands.INPUT_POS.value, [Model.Kinematic_Model(coords, rotations, translations)[0][0][2], 0, 0], 'fhh')
#            #BL
            odrive_can_cmd(Joint.BL_hip.value, Commands.INPUT_POS.value, [Model.Kinematic_Model(coords, rotations, translations)[3][0][0], 0, 0], 'fhh')
            odrive_can_cmd(Joint.BL_upper.value, Commands.INPUT_POS.value, [Model.Kinematic_Model(coords, rotations, translations)[3][0][1], 0, 0], 'fhh')
            odrive_can_cmd(Joint.BL_lower.value, Commands.INPUT_POS.value, [Model.Kinematic_Model(coords, rotations, translations)[3][0][2], 0, 0], 'fhh')
#            #BR
            odrive_can_cmd(Joint.BR_hip.value, Commands.INPUT_POS.value, [Model.Kinematic_Model(coords, rotations, translations)[2][0][0], 0, 0], 'fhh')
            odrive_can_cmd(Joint.BR_upper.value, Commands.INPUT_POS.value, [Model.Kinematic_Model(coords, rotations, translations)[2][0][1], 0, 0], 'fhh')
            odrive_can_cmd(Joint.BR_lower.value, Commands.INPUT_POS.value, [Model.Kinematic_Model(coords, rotations, translations)[2][0][2], 0, 0], 'fhh')
        controller_state_available.clear()

main_thread = threading.Thread(target=main)
server_thread = threading.Thread(target=socket_server)
main_thread.start()
server_thread.start()

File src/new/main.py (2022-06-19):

from XInput import *
import numpy as np
import odrive
from odrive.enums import *

from Gaits import *
import KinematicModel
import IK

FR = odrive.find_any(serial_number='207D348C5748')
FL = odrive.find_any(serial_number='2074347E5748')
BR = odrive.find_any(serial_number='207D34885748')
BL = odrive.find_any(serial_number='207D34945748')

# frontHip = odrive.find_any(serial_number=)
# backHip = odrive.find_any(serial_number='206F37915753')

# https://stackoverflow.com/questions/8508799/bit-masking-in-python

zTrans = 0
T = 0.00

coords = np.array([[0.00, -0.18, -0.20],   #FR x y z
                   [0.00,  0.18, -0.20],   #FL
                   [0.00, -0.18, -0.20],   #BR
                   [0.00,  0.18, -0.20]])  #BL

rotations = np.array([0.00, 0.00, 0.00]) #roll pitch yaw
translation = np.array([0.00, 0.00, 0.00])

while True:
    for event in get_events():
        if event.type == EVENT_BUTTON_PRESSED:

            if event.button == "BACK":
                print('Shutting Motors Off...')

                FR.axis0.requested_state = AXIS_STATE_IDLE
                FR.axis1.requested_state = AXIS_STATE_IDLE

                FL.axis0.requested_state = AXIS_STATE_IDLE
                FL.axis1.requested_state = AXIS_STATE_IDLE

                BR.axis0.requested_state = AXIS_STATE_IDLE
                BR.axis1.requested_state = AXIS_STATE_IDLE
                #
                BL.axis0.requested_state = AXIS_STATE_IDLE
                BL.axis1.requested_state = AXIS_STATE_IDLE

                # backHip.axis0.requested_state = AXIS_STATE_IDLE
                # backHip.axis1.requested_state = AXIS_STATE_IDLE

                time.sleep(0.1)

            elif event.button == "START":
                print('Starting Motors...')

                FR.axis0.requested_state = AXIS_STATE_CLOSED_LOOP_CONTROL
                FR.axis1.requested_state = AXIS_STATE_CLOSED_LOOP_CONTROL

                FL.axis0.requested_state = AXIS_STATE_CLOSED_LOOP_CONTROL
                FL.axis1.requested_state = AXIS_STATE_CLOSED_LOOP_CONTROL

                BR.axis0.requested_state = AXIS_STATE_CLOSED_LOOP_CONTROL
                BR.axis1.requested_state = AXIS_STATE_CLOSED_LOOP_CONTROL
                #
                BL.axis0.requested_state = AXIS_STATE_CLOSED_LOOP_CONTROL
                BL.axis1.requested_state = AXIS_STATE_CLOSED_LOOP_CONTROL

                # backHip.axis0.requested_state = AXIS_STATE_CLOSED_LOOP_CONTROL
                # backHip.axis1.requested_state = AXIS_STATE_CLOSED_LOOP_CONTROL

                time.sleep(0.1)

            elif event.button == "A" and zTrans <= 0.15:
                print("A")
                zTrans += 0.008
                # translation[2] += 0.008
                coords[0][2] += 0.008
                coords[1][2] += 0.008
                coords[2][2] += 0.008
                coords[3][2] += 0.008

                print(coords[0][2], zTrans)
                time.sleep(0.1)

            elif event.button == "B" and zTrans >= -0.15:
                print("B")
                zTrans -= 0.008
                # translation[2] -= 0.008
                coords[0][2] -= 0.008
                coords[1][2] -= 0.008
                coords[2][2] -= 0.008
                coords[3][2] -= 0.008

                print(coords[0][2], zTrans)
                time.sleep(0.1)

            while event.button == "X":
                print("Move in Place")

                coords = np.array([[0.00, -0.18, -0.15],   #FR x y z
                                   [0.00,  0.18, -0.20],   #FL
                                   [0.00, -0.18, -0.20],   #BR
                                   [0.00,  0.18, -0.15]])  #BL

                time.sleep(0.5)

                coords = np.array([[0.00, -0.18, -0.20],   #FR x y z
                                   [0.00,  0.18, -0.15],   #FL
                                   [0.00, -0.18, -0.15],   #BR
                                   [0.00,  0.18, -0.20]])  #BL

                time.sleep(0.5)

            else:
                break

        elif event.type == EVENT_STICK_MOVED:
            if event.stick == LEFT:
                speed = get_thumb_values(get_state(event.user_index))[0][1] / 20
                print("Move At Speed: " + str(speed))
                if T <= 0:
                    T = 2
                elif T <= 1:
                    coords[0][0], coords[0][2] = bezier(T) #FR
                    coords[0][2] = coords[0][2] + zTrans

                    coords[3][0], coords[3][2] = bezier(T) #BL
                    coords[3][2] = coords[3][2] + zTrans

                    coords[1][0], coords[1][2] = (-0.4/(2-T) + 0.3), -0.4 + zTrans #FL

                    coords[2][0], coords[2][2] = (-0.4/(2-T) + 0.3), -0.4 + zTrans #BR

                    FR.axis0.controller.input_pos = KinematicModel.Kinematic_Model(coords, rotations, translation)[0][0][1]
                    FR.axis1.controller.input_pos = KinematicModel.Kinematic_Model(coords, rotations, translation)[0][0][2]

                    FL.axis0.controller.input_pos = KinematicModel.Kinematic_Model(coords, rotations, translation)[1][0][1]
                    FL.axis1.controller.input_pos = KinematicModel.Kinematic_Model(coords, rotations, translation)[1][0][2]

                    BR.axis0.controller.input_pos = KinematicModel.Kinematic_Model(coords, rotations, translation)[2][0][1]
                    BR.axis1.controller.input_pos = KinematicModel.Kinematic_Model(coords, rotations, translation)[2][0][2]

                    BL.axis0.controller.input_pos = KinematicModel.Kinematic_Model(coords, rotations, translation)[3][0][1]
                    BL.axis1.controller.input_pos = KinematicModel.Kinematic_Model(coords, rotations, translation)[3][0][2]

                    time.sleep(0.001)
                    T += speed
                elif T > 1 and T <= 2:
                    coords[1][0], coords[1][2] = bezier(T-1)
                    coords[1][2] = coords[1][2] + zTrans

                    coords[2][0], coords[2][2] = bezier(T-1) #FR
                    coords[2][2] = coords[2][2] + zTrans

                    coords[0][0], coords[0][2] = 0.4/T - 0.3, -0.4 + zTrans #BR

                    coords[3][0], coords[3][2] = 0.4/T - 0.3, -0.4 + zTrans #BR

                    FR.axis0.controller.input_pos = KinematicModel.Kinematic_Model(coords, rotations, translation)[0][0][1]
                    FR.axis1.controller.input_pos = KinematicModel.Kinematic_Model(coords, rotations, translation)[0][0][2]

                    FL.axis0.controller.input_pos = KinematicModel.Kinematic_Model(coords, rotations, translation)[1][0][1]
                    FL.axis1.controller.input_pos = KinematicModel.Kinematic_Model(coords, rotations, translation)[1][0][2]
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

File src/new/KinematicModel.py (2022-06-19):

import numpy as np
import IK
import Matrices

L = 0.52
W = 0.15
coxa = 0.186
femur = 0.29
tibia = 0.31

def Kinematic_Model(coord, rotation, translation):
    oriToFR = np.array([ L/2, -W/2, 0])
    oriToFL = np.array([ L/2,  W/2, 0])
    oriToBR = np.array([-L/2, -W/2, 0])
    oriToBL = np.array([-L/2,  W/2, 0])

    oriToFRNew = Matrices.transform(oriToFR, rotation, translation)
    oriToFLNew = Matrices.transform(oriToFL, rotation, translation)
    oriToBRNew = Matrices.transform(oriToBR, rotation, translation)
    oriToBLNew = Matrices.transform(oriToBL, rotation, translation)

    FROffset = -oriToFRNew + oriToFR
    FLOffset = -oriToFLNew + oriToFL
    BROffset = -oriToBRNew + oriToBR
    BLOffset = -oriToBLNew + oriToBL

    FRCoord = np.array([coord[0][0], coord[0][1], coord[0][2]])
    FLCoord = np.array([coord[1][0], coord[1][1], coord[1][2]])
    BRCoord = np.array([coord[2][0], coord[2][1], coord[2][2]])
    BLCoord = np.array([coord[3][0], coord[3][1], coord[3][2]])

    FRCoordNew = FRCoord + FROffset
    FLCoordNew = FLCoord + FLOffset
    BRCoordNew = BRCoord + BROffset
    BLCoordNew = BLCoord + BLOffset

    FRAngles = np.rad2deg(IK.solve_R(FRCoordNew, coxa, femur, tibia))
    FLAngles = np.rad2deg(IK.solve_L(FLCoordNew, coxa, femur, tibia))
    BRAngles = np.rad2deg(IK.solve_L(BRCoordNew, coxa, femur, tibia))
    BLAngles = np.rad2deg(IK.solve_R(BLCoordNew, coxa, femur, tibia))

    FRAngles[0] = (FRAngles[0]+90) * 1/36
    FRAngles[1] = (FRAngles[1]) * 1/36 #convert to rotations and adjusted for gearbox
    FRAngles[2] = (FRAngles[2]) * 7/144

    FLAngles[0] = (FLAngles[0]+90) * 1/36
    FLAngles[1] = (FLAngles[1]) * 1/36 #convert to rotations and adjusted for gearbox
    FLAngles[2] = (FLAngles[2]) * 7/144

    BRAngles[0] = (BRAngles[0]+90) * 1/36
    BRAngles[1] = (BRAngles[1]) * 1/36 * 8/10 #convert to rotations and adjusted for gearbox
    BRAngles[2] = (BRAngles[2]) * 7/144

    BLAngles[0] = (BLAngles[0]+90) * 1/36
    BLAngles[1] = (BLAngles[1]) * 1/36 #convert to rotations and adjusted for gearbox
    BLAngles[2] = (BLAngles[2]) * 7/144

    allAnglesString = np.array([[FRAngles], [-FLAngles], [BRAngles], [-BLAngles]])

    return allAnglesString

# coords = np.array([[0, -0.18, -0.3],   #FR
#                    [0,  0.18, -0.3],   #FL
#                    [0, -0.18, -0.3],   #BR
#                    [0,  0.18, -0.3]])  #BL
#
# rotations = np.array([0,0,-0.01])
# translation = np.array([0,0,0])
#
# print(Kinematic_Model(coords, rotations, translation))

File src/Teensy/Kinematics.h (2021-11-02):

#include "math.h"

#define PI 3.14159265

const float upper_leg_length = 28;
const float lower_leg_length = 28;

const int coxa = 0;
const float femur = 28;
const float tibia = 28; // measurements in cm


class KinematicModel{
public:
    float domainCheck(float &D){
        if(D > 1 || D < -1){
            if(D > 1){
                D = 0.99;
                return D;
            }
            else if(D < -1){
                D = -0.99;
                return D;
            }
        }
        else{
            return D;
        }
    }

    float LegKinematicModel(float x, float y, float z, int sign, float &upper_angle, float &lower_angle, float &hip_angle){
        float D = (pow(y, 2) + pow(z, 2) - pow(coxa, 2) + pow(x, 2) - pow(femur, 2) - pow(tibia, 2))/(2 * tibia * femur);
        D = domainCheck(D);
        lower_angle = (sign * atan2(sqrt(1 - pow(D, 2)), D)) * 180/PI;
        hip_angle = (-atan2(-z, y) - atan2((sqrt(pow(y, 2) + pow(-z, 2) - pow(coxa, 2))), -coxa)) * 180/PI;
        upper_angle = (atan2(x, sqrt(pow(y, 2) + pow(z, 2) - pow(coxa, 2)) - atan2(tibia * sin(lower_angle), femur + tibia * cos(lower_angle)))) * 180/PI;
    }

    float angle2Rot(float angle){
        float rot = angle * 10/360;
        return rot;
    }
};

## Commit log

2022-04-01 Inverse Kinematics (Python)
2022-04-02 add initial cut of cpp implementation
2022-08-16 Actuator V2
    added second iteration of the actuator :)
    [Encoder Holder 8308.stl, Encoder Holder 8318.stl, Lower Leg Actuator Holder 8318 v3.stl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]
2022-08-17 Added pybullet simulation
    [BL_Joint1.stl, BL_Lower_Leg1.stl, BL_Upper_Leg1.stl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]
